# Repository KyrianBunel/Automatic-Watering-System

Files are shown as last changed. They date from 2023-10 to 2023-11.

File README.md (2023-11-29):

# Automatic-Watering-System
Esp32-based automatic irrigation system capable of controlling up to 6 different zones independently

# Features :
- Create a wifi access point to enter wifi information
- Automatically connects to the local network if available
- Compatible with a weather station included in the project to collect temperature, humidity and brightness data, also features a rain sensor
- Able to use up to 3 soil moisture sensors
- Controllable through a web page (LOCAL_IP_ADDRESS/accueil ex : 192.168.1.10/accueil)
    - 3 operating modes :
  
          - MANU -> allows manual control of the 6 valves independently; once the selected valve is active, it can be deactivated only if the user does it manually.
          - AUTO -> uses weather station and soil moisture sensors to automatically trigger a 15-minute watering cycle.
          - PROG -> allows the user to enter information such as watering start and end date, watering duration, recurrence and watering time for each valve via a form.
- Ability to view the current program and sensors values via a dashboard page (LOCAL_IP_ADDRESS/dashboard ex : 192.168.1.10/dashboard)
- Compatible with arduino OTA (update through the local network)
- Automatic watering stop in case of rain (except in MANU mode)
- Transmits sensor data hourly to a Google sheet to create a database

# Future improvements :
- Web pages :
    - Add a settings page
    - Add the possibility of choosing the language (French only for the moment)
    - Add the ability to modify the ID of Google Sheet page in the web interface
    - Add the possibility to modify the number of valve used
- Database :
    - Improve the data sent as the total duration of watering during the last hour to be able to deduct the cost of watering per month and per year
- PCB :
    - Upgrade to an ESP32-WROOM-32UE to add an external antenna and increase the WiFi connection range
    - Move mounting holes & components away from board edge
    - Increase mounting hole size to M3
    - Move decoupling capacitors closer to power supply pins
    - Add a differential pair to the usb port
    - Improve the DC-DC Buck Converter design (produce heat + noise coming from the inductance during current peaks)

# How to start up :
### Home page & Dashboard
- Download the code and upload it to the ESP 32
Capture d’écran 2023-11-27 à 16 22 07

- Press the reset button on the PCB

- Go to the phone settings and connect to the Wifi network: ArrosageAUTO_XXX
- Wait for a web page to open. If the web page doesn't open automatically, go to your browser and type "192.168.4.1"
- Click on "Configure WiFi"
- select your wifi network and enter your password
- Click on "Save"
- And you're done, you can now access the following web pages: LOCAL_IP_ADDRESS/accueil & LOCAL_IP_ADDRESS/dashboard

### Dadabase
- Download the following file [here](https://docs.google.com/spreadsheets/d/1MzfrYDloWlxmfWAgQVE4hzFRyIgfXsLG/edit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) and place it in your personal directory
- Click on "file" -> "save in google sheet format"
Capture d’écran 2023-11-27 à 15 38 50

- Then click on "extensions" -> "apps script" and paste the following code :
Capture d’écran 2023-11-27 à 15 45 44

```
var sheet_id = "YOUR_GOOGLE_SHEET_ID";
var sheet_name = "ArrosageAUTO_data";
function doGet(e){
var ss = SpreadsheetApp.openById(sheet_id);
var sheet = ss.getSheetByName(sheet_name);

var date = e.parameter.date;
var temperature = e.parameter.temperature;
var humidite = e.parameter.humidite;
var luminosite = e.parameter.luminosite;
var moistureSensor1 = e.parameter.moistureSensor1;
var moistureSensor2 = e.parameter.moistureSensor2;
var moistureSensor3 = e.parameter.moistureSensor3;

sheet.appendRow([date,temperature, humidite, luminosite, moistureSensor1, moistureSensor2, moistureSensor3]);
}
```

- Click on "deploy" -> "New deployment" add a description and click "OK"
Capture d’écran 2023-11-27 à 15 22 52

# Additional material required :
- DHT22 temperature and humidity sensor
- Capacitive moisture sensor (3 maximum)
- 9V 24V tranformer (depending on your instlation)
- Rain sensor
- Wi-Fi network (a powerful network to allow pages to load faster)

# Web pages :
### Home page & Dashboard
Capture d’écran 2023-11-24 à 09 25 02

### Extract from the database
Capture d’écran 2023-11-24 à 09 27 08

(the data displayed is random, as no sensor was connected to the board)

# PCB :
Capture d’écran 2023-11-24 à 10 55 46

You can directly order the PCB via this link: https://www.pcbway.com/project/shareproject/Automatic_Watering_System_7e1279b2.html

# Weather station :

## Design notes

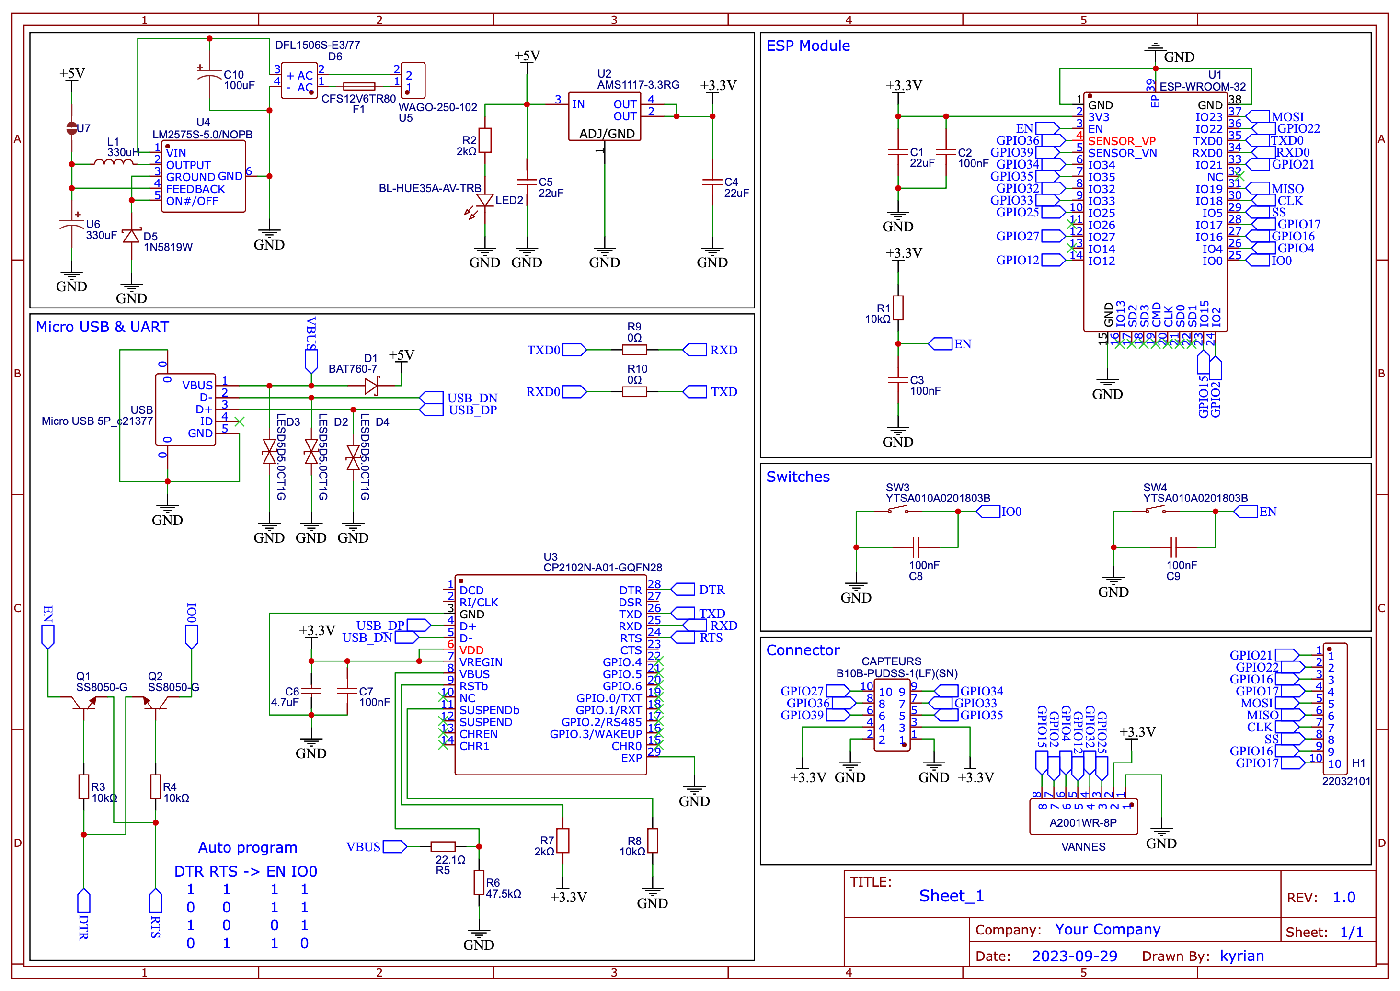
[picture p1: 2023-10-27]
PCB/Schematic_Arrosage automatique_2023-10-27.png

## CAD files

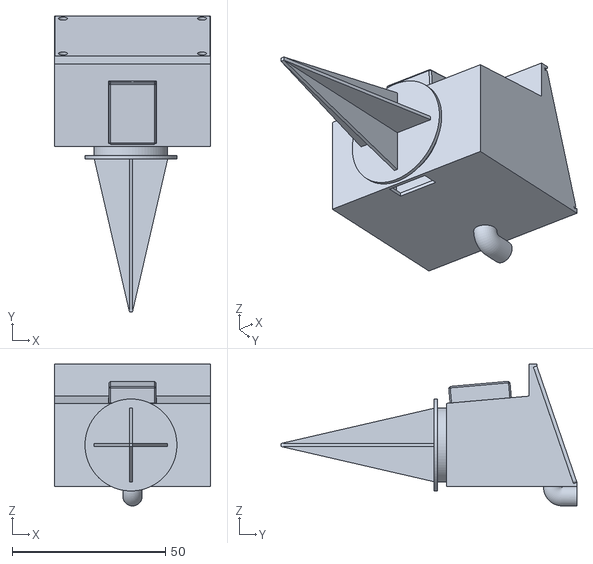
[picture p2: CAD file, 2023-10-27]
3D Models/weather station/assemblage v7.stl
51.0 x 96.6 x 46.3

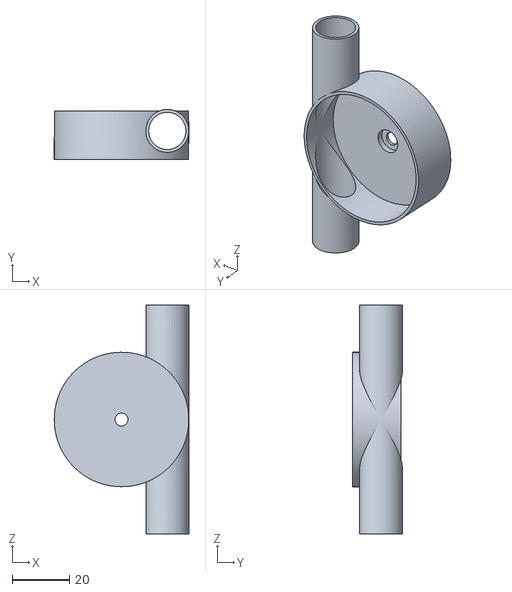
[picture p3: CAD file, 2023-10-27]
3D Models/flow meter/case V2 v1.stl
47.0 x 17.5 x 80.0

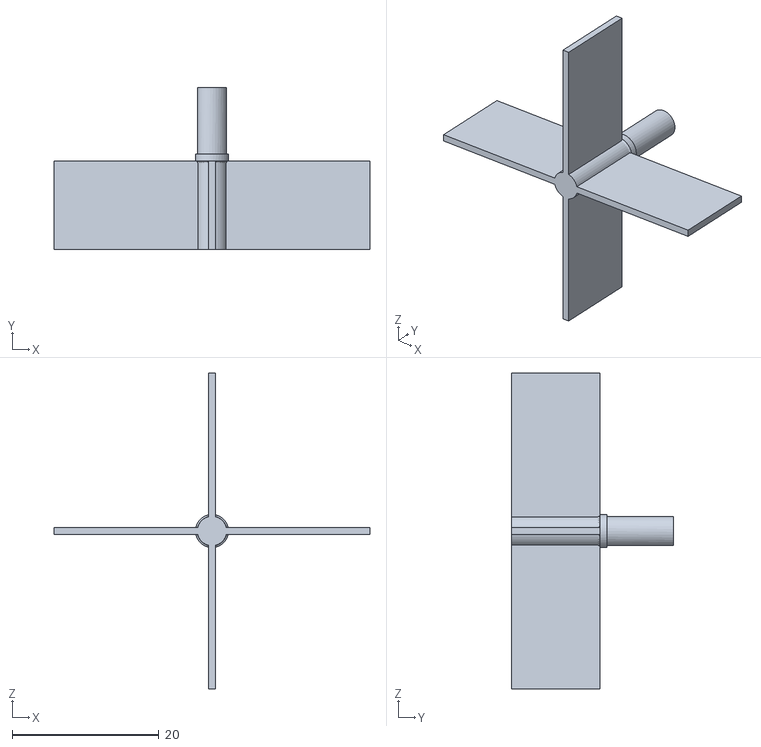
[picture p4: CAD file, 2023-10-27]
3D Models/flow meter/prop V2 v4.stl
43.0 x 22.0 x 43.0

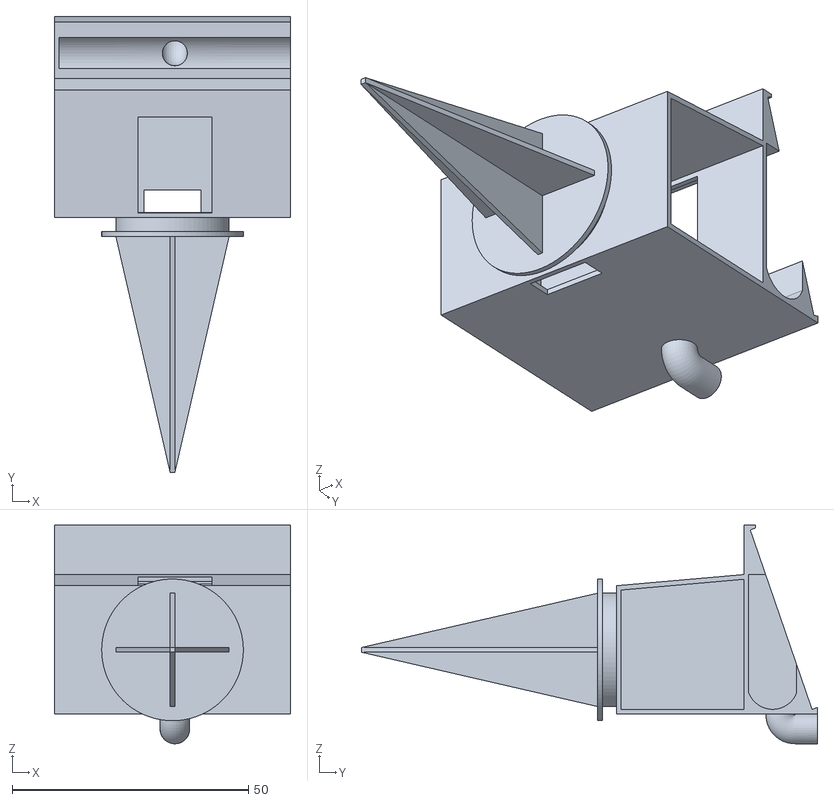
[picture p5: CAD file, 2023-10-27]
3D Models/weather station/station météo v7.stl
50.0 x 96.6 x 46.3

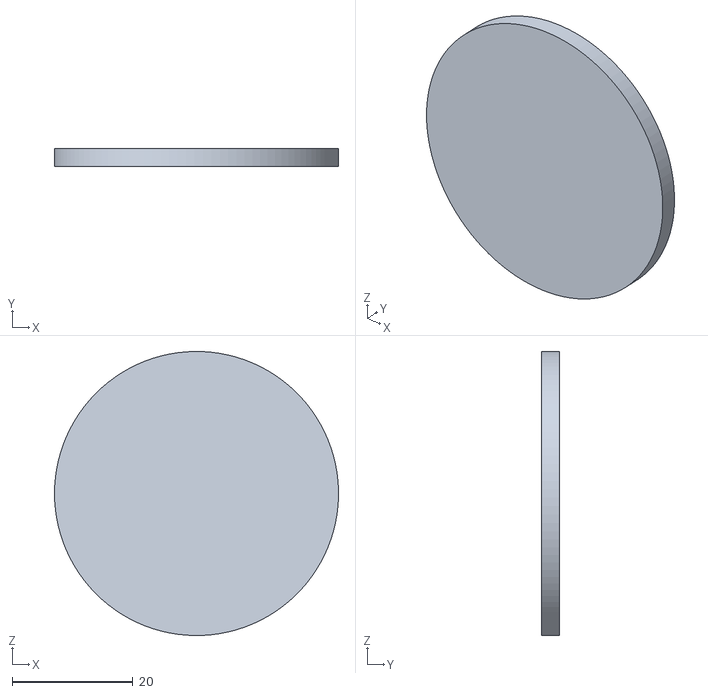
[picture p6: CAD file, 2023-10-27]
3D Models/flow meter/COVER V2 v1.stl
47.0 x 3.00 x 47.0

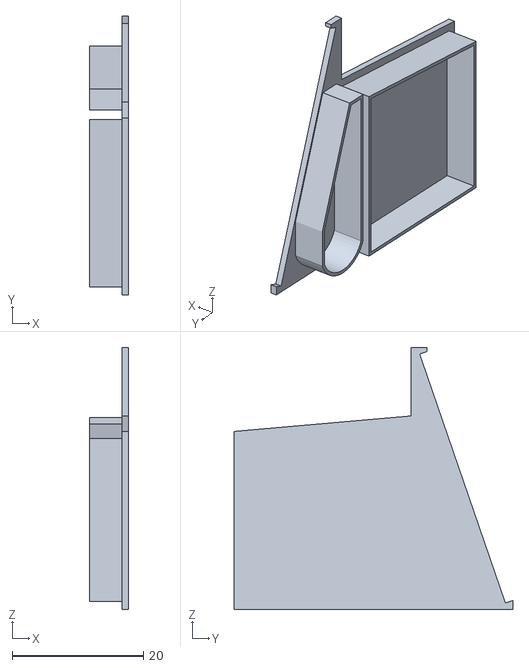
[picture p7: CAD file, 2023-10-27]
3D Models/weather station/side v3.stl
6.00 x 42.6 x 40.0

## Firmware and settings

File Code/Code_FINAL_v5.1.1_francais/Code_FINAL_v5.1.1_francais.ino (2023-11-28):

/*

...............................BIBLIOTHEQUES...............................

*/
#include <WiFi.h>
#include <WiFiManager.h>  // https://github.com/tzapu/WiFiManager
#include <WebServer.h>
#include <ArduinoOTA.h>
#include "DHT.h"
#include <HTTPClient.h>
#include "time.h"

// Google script ID
String GOOGLE_SCRIPT_ID = "YOUR_GOOGLESHEET_ID";  // change Gscript ID

#define DHTPIN 27
#define DHTTYPE DHT22

DHT dht(DHTPIN, DHTTYPE);
struct tm timeinfo;

/*

...............................VARIABLES...............................

*/
String version_logiciel = "5.1.1_fr";    // version du logiciel

const char *ssid = "****";            // SSID WiFI
const char *password = "****";        // Mot de passe WiFi

WebServer server(80);  // Server sur le port 80 (page web)

const char *ntpServer = "pool.ntp.org";  // adresse du serveur NTP
const long gmtOffset_sec = 3600 * 2;     // fuseau horraire (paris)
const int daylightOffset_sec = 3600 * 0;

int SeuilHumidite = 10;  // humididé dans le sol
float SeuilTemperatureMAX = 25.00;
float SeuilTemperatureMIN = 15.00;
int SeuilHumidity = 40.00;  // humidité dans l'air

int TimerAUTO = 0;       // Mesurer le temps d'arrosage en mode AUTO
int delayAUTO = 600000;  // temps d'arrosage en mode AUTO (en ms)
int ModeAuto = 1;        // activation ou non de l'arrosage en mode auto
int JourArrosage;

int bpVanne1 = 0;  // Bouton vanne 1 du mode MANU
int bpVanne2 = 0;  // Bouton vanne 2 du mode MANU
int bpVanne3 = 0;  // Bouton vanne 3 du mode MANU

int MoistureSensor1;  // Capteur d'humidité dans le sol 1
int MoistureSensor2;  // Capteur d'humidité dans le sol 2
int MoistureSensor3;  // Capteur d'humidité dans le sol 3

int pluie;        // Valeur du capteur de pluie
String StrPluie;  // Valeur du capteur de pluie (True/False)

float humidity;     // Valeur humidité
float temperature;  // Valeur température

int luminosite;  // Valeur du capteur de luminosité

int Hour;   // heure actuelle
int Min;    // minute actuelle
int Sec;    // seconde actuelle
int Day;    // jour actuel
int Month;  // mois actuel
int Year;   // année actuelle

int en;

#define vanne1 12        // Vanne 1 sur GPIO12 de l'esp
#define vanne2 32        // Vanne 2 sur GPIO32 de l'esp
#define vanne3 25        // Vanne 3 sur GPIO25 de l'esp
#define CapteurPluie 36  // Capteur de pluie sur GPIO36 de l'esp

char StrHour[40];                                                          // formattage de l'heure en chaîne de caractère
char StrDate[40];                                                          // formattage de la date en chaîne de caractère
char HtmlON[50] = "<div class='rectangleON'>ON</div>";                     // afficher un carré vert marqué ON
char HtmlOFF[50] = "<div class='rectangleOFF'>OFF</div>";                  // afficher un carré rouge marqué OFF
char HtmlDISABLED[50] = "<div class='rectangleDISABLED'>DÉSACTIVÉ</div>";  // afficher un carré violet marqué DISABLED
char HtmlZone1[50];                                                        // afficher état de la zone 1 dans le dashboard
char HtmlZone2[50];                                                        // afficher état de la zone 2 dans le dashboard
char HtmlZone3[50];                                                        // afficher état de la zone 3 dans le dashboard

float usagePercentage;  // Utilisation de la mémoire en %

String mode = "MANU";  // Initialisation de la variable "mode" (valeur par défaut = MANU)

String HTMLtabl;  // Initialisation de la viriable tabl (calendrier)

/* Date de début */
String StrDateDebut;   // enregistrer la date de début rentré dans le formulaire
String StrStartDay;    // Jour de départ (string)
String StrStartMonth;  // Mois de départ (string)
String StrStartYear;   // Année de départ (string)
int StartDay;          // Jour de départ (int)
int StartMonth;        // Mois de départ (int)
int StartYear;         // Année de départ (int)

/* Date de fin */
String StrDateFin;   // enregistrer la date de début rentré dans le formulaire
String StrEndDay;    // Jour de fin (string)
String StrEndMonth;  // Mois de fin (string)
String StrEndYear;   // Année de fin (string)
int EndDay;          // Jour de fin (int)
int EndMonth;        // Mois de fin (int)
int EndYear;         // Année de fin (int)

String StrDuree;  // Dureé du programme (string)
int duree;        // Dureé du programme (int)

String StrRecurrence;  // Récurence (string)
int recurrence;        // Récurence (int)

/* Zone 1 */
String StrZone1;  // Activation de la zone 1 ou non
String StrDebut1;
String StrHeureDebut1;   // Heure de début (string)
String StrMinDebut1;     // Minute de début (string)
char IntervalZone1[40];  // interval d'arrosage (chaîne de carractère)
int HeureDebut1;         // Heure de début (int)
int MinDebut1;           // Minute de début (int)
int EndMin1;             // Minute de fin (int)
int EndHour1;            // Heure de fin (int)

/* Zone 2 */
String StrZone2;  // Activation de la zone 2 ou non
String StrDebut2;
String StrHeureDebut2;   // Heure de début (string)
String StrMinDebut2;     // Minute de début (string)
char IntervalZone2[40];  // interval d'arrosage (chaîne de carractère)
int HeureDebut2;         // Heure de début (int)
int MinDebut2;           // Minute de début (int)
int EndMin2;             // Minute de fin (int)
int EndHour2;            // Heure de fin (int)

/* Zone 3 */
String StrZone3;  // Activation de la zone 3 ou non
String StrDebut3;
String StrHeureDebut3;   // Heure de début (string)
String StrMinDebut3;     // Minute de début (string)
char IntervalZone3[40];  // interval d'arrosage (chaîne de carractère)
int HeureDebut3;         // Heure de début (int)
int MinDebut3;           // Minute de début (int)
int EndMin3;             // Minute de fin (int)
int EndHour3;            // Heure de fin (int)

/*

...............................FONCTIONS...............................

*/
/* Calculer le premier jour du mois (Algorithme de Zeller) */
int calculerPremierJour(int annee, int mois) {
  int a = (14 - mois) / 12;
  int y = annee - a;
  int m = mois + 12 * a - 2;
  int jour = (1 + y + y / 4 - y / 100 + y / 400 + (31 * m) / 12) % 7;
  jour--;
  return jour;  // Retourne le jour de la semaine
}

/* Calculer le nombre de jours en fonction du mois */
int getNumberOfDays(int year, int month) {
  switch (month) {
    case 1:   // Janvier
    case 3:   // Mars
    case 5:   // Mai
    case 7:   // Juillet
    case 8:   // Août
    case 10:  // Octobre
    case 12:  // Décembre
      return 31;
    case 4:   // Avril
    case 6:   // Juin
    case 9:   // Septembre
    case 11:  // Novembre
      return 30;
    case 2:  // Février
      if ((year % 4 == 0 && year % 100 != 0) || (year % 400 == 0)) {
        return 29;  // Année bissextile
      } else {
        return 28;
      }
    default:
      return 0;  // Mois invalide
  }
}

void sendData() {
  String urlFinal = "https://script.google.com/macros/s/" + GOOGLE_SCRIPT_ID + "/exec?" + "date=" + Day + "/" + Month + "/" + Year + "_" + String(Hour) + ":" + String(Min) + ":" + String(Sec) + "&temperature=" + String(temperature) + "&humidite=" + String(humidity) + "&luminosite=" + String(luminosite) + "&moistureSensor1=" + String(MoistureSensor1) + "&moistureSensor2=" + String(MoistureSensor2) + "&moistureSensor3=" + String(MoistureSensor3);
  HTTPClient http;
  http.begin(urlFinal.c_str());
  http.setFollowRedirects(HTTPC_STRICT_FOLLOW_REDIRECTS);
  int httpCode = http.GET();
  http.end();
}

/* Gestion du bouton "MANU" */
void handleMANU() {
  mode = "MANU";
  server.sendHeader("Location", "/accueil");
  server.send(302, "text/plain", "");  // Envoi d'un code de statut 302 (Redirection) sans contenu
}

/* Gestion du bouton "AUTO" */
void handleAUTO() {
  mode = "AUTO";
  bpVanne1 = 0;
  bpVanne2 = 0;
  bpVanne3 = 0;
  server.sendHeader("Location", "/accueil");
  server.send(302, "text/plain", "");  // Envoi d'un code de statut 302 (Redirection) sans contenu
}

/* Gestion du bouton "PROG" */
void handlePROG() {
  mode = "PROG";
  bpVanne1 = 0;
  bpVanne2 = 0;
  bpVanne3 = 0;
  server.sendHeader("Location", "/accueil");
  server.send(302, "text/plain", "");  // Envoi d'un code de statut 302 (Redirection) sans contenu
}

/* Gestion du bouton Vanne 1 du mode MANU (activation/déactivation de l'arrosage) */
void handleVanne1() {
  if (bpVanne1 == 0 && mode == "MANU") {
    bpVanne1 = 1;
  } else
    bpVanne1 = 0;
  server.sendHeader("Location", "/accueil");
  server.send(302, "text/plain", "");  // Envoi d'un code de statut 302 (Redirection) sans contenu
}

/* Gestion du bouton Vanne 2 du mode MANU (activation/déactivation de l'arrosage) */
void handleVanne2() {
  if (bpVanne2 == 0) {
    bpVanne2 = 1;
  } else
    bpVanne2 = 0;
  server.sendHeader("Location", "/accueil");
  server.send(302, "text/plain", "");  // Envoi d'un code de statut 302 (Redirection) sans contenu
}

/* Gestion du bouton Vanne 3 du mode MANU (activation/déactivation de l'arrosage)*/
void handleVanne3() {
  if (bpVanne3 == 0) {
    bpVanne3 = 1;
  } else
    bpVanne3 = 0;
  server.sendHeader("Location", "/accueil");
  server.send(302, "text/plain", "");  // Envoi d'un code de statut 302 (Redirection) sans contenu
}

/*  Gestion du formulaire du mode PROG  */
void handleSubmit() {
  // Récupération des valeurs du formulaire
  StrDuree = server.arg("duree");
  StrDateDebut = server.arg("dateDebut");
  StrDateFin = server.arg("dateFin");
  StrRecurrence = server.arg("recurrence");
  StrZone1 = server.arg("zone1");
  StrZone2 = server.arg("zone2");
  StrZone3 = server.arg("zone3");
  StrDebut1 = server.arg("heureDebut1");
  StrDebut2 = server.arg("heureDebut2");
  StrDebut3 = server.arg("heureDebut3");



  /* Date de début (conversion str -> int) */
  StrStartDay = StrDateDebut.substring(8, 10);
  StrStartMonth = StrDateDebut.substring(5, 7);
  StrStartYear = StrDateDebut.substring(0, 4);
  StartDay = StrStartDay.toInt();
  StartMonth = StrStartMonth.toInt();
  StartYear = StrStartYear.toInt();

  /* Date de fin (conversion str -> int) */
  StrEndDay = StrDateFin.substring(8, 10);
  StrEndMonth = StrDateFin.substring(5, 7);
  StrEndYear = StrDateFin.substring(0, 4);
  EndDay = StrEndDay.toInt();
  EndMonth = StrEndMonth.toInt();
  EndYear = StrEndYear.toInt();

  /* Durée du programme (conversion str -> int)*/
  duree = StrDuree.toInt();

  /* Récurrence (conversion str -> int) */
  recurrence = StrRecurrence.toInt();

  /* Zone 1 (conversion str -> int) */
  StrHeureDebut1 = StrDebut1.substring(0, 2);
  StrMinDebut1 = StrDebut1.substring(3, 5);
  HeureDebut1 = StrHeureDebut1.toInt();
  MinDebut1 = StrMinDebut1.toInt();

  /* Zone 2 (conversion str -> int) */
  StrHeureDebut2 = StrDebut2.substring(0, 2);
  StrMinDebut2 = StrDebut2.substring(3, 5);
  HeureDebut2 = StrHeureDebut2.toInt();
  MinDebut2 = StrMinDebut2.toInt();

  /* Zone 3 (conversion str -> int) */
  StrHeureDebut3 = StrDebut3.substring(0, 2);
  StrMinDebut3 = StrDebut3.substring(3, 5);
  HeureDebut3 = StrHeureDebut3.toInt();
  MinDebut3 = StrMinDebut3.toInt();

  /* End Min */
  EndMin1 = MinDebut1 + duree;
  EndMin2 = MinDebut2 + duree;
  EndMin3 = MinDebut3 + duree;

  /* End Hour */
  EndHour1 = HeureDebut1;
  EndHour2 = HeureDebut2;
  EndHour3 = HeureDebut3;

  if (EndMin1 >= 60) {
    EndMin1 = EndMin1 - 60;
    EndHour1++;
  }
  if (EndMin2 >= 60) {
    EndMin2 = EndMin2 - 60;
    EndHour2++;
  }
  if (EndMin3 >= 60) {
    EndMin3 = EndMin3 - 60;
    EndHour3++;
  }

  /* Formattage interval d'arrosage zone 1 */
  if (StrZone1 == "on")
    sprintf(IntervalZone1, "%s""%s""%d""%s""%d",StrDebut1, "-", EndHour1, ":", EndMin1);
  else
    sprintf(IntervalZone1, "%s", " ");

  /* Formattage interval d'arrosage zone 2 */
  if (StrZone2 == "on")
    sprintf(IntervalZone2, "%s""%s""%d""%s""%d",StrDebut2, "-", EndHour2, ":", EndMin2);
  else
    sprintf(IntervalZone2, "%s", " ");

  /* Formattage interval d'arrosage zone 3 */
  if (StrZone3 == "on")
    sprintf(IntervalZone3, "%s""%s""%d""%s""%d",StrDebut3, "-", EndHour3, ":", EndMin3);
  else
    sprintf(IntervalZone3, "%s", " ");

  /* Récupération du mois et de l'année actuelle sur le server NTP */
  Month = timeinfo.tm_mon + 1;
  Year = timeinfo.tm_year + 1900;

  /* Génération du calendrier du mois en cours */
  int premierJour = calculerPremierJour(Year, Month);

  HTMLtabl = "";
  HTMLtabl += "<h2>Planning d'arrosage</h2> <table> <thead><tr> <th>Lun</th> <th>Mar</th> <th>Mer</th> <th>Jeu</th> <th>Ven</th> <th>Sam</th> <th>Dim</th> </tr> </thead> <tbody>";
  int tablDay = 1;
  int offset = 1;
  int numberOfDays = getNumberOfDays(Year, Month);

  int MaxIter;
  if (premierJour == 6 && numberOfDays == 30)
    MaxIter = 7;
  else
    MaxIter = 6;

  for (int a = 1; a < MaxIter; a++) {
    HTMLtabl += "<tr>";
    for (int i = 1; i < 8; i++) {
      int modulo = tablDay % recurrence;
      if (premierJour >= offset || tablDay > numberOfDays) {
        HTMLtabl += "<td></td>";
      } else if (modulo == 0 && tablDay >= StartDay && tablDay <= EndDay) {
        HTMLtabl += "<td class='highlight'>";  // mettre la case en surbrillance
        HTMLtabl += tablDay;
        HTMLtabl += "</td>";
        tablDay++;
      } else {
        HTMLtabl += "<td>";
        HTMLtabl += tablDay;
        HTMLtabl += "</td>";
        tablDay++;
      }
      offset++;
    }
    HTMLtabl += "</tr>";
  }
  server.sendHeader("Location", "/accueil");
  server.send(302, "text/plain", "");  // Envoi d'un code de statut 302 (Redirection) sans contenu
}

/*

...............................PAGES WEB...............................
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
void loop() {

  server.handleClient();  // Maintenir le client actif (pages web)
  ArduinoOTA.handle();    // Maintenir le client actif (OTA)

  pluie = analogRead(CapteurPluie);  // lecture de la valeur du capteur de pluie + gestion du string pour affichage au dashboard
  if (pluie >> 1)
    StrPluie = "True";
  else
    StrPluie = "False";

  MoistureSensor1 = map(analogRead(35), 0, 4095, 100, 0);  // lecture de la valeur de capteur de pluie + convertion 0,4095->0,100 (%)
  MoistureSensor2 = map(analogRead(33), 0, 4095, 100, 0);  // lecture de la valeur de capteur de pluie + convertion 0,4095->0,100 (%)
  MoistureSensor3 = map(analogRead(34), 0, 4095, 100, 0);  // lecture de la valeur de capteur de pluie + convertion 0,4095->0,100 (%)
  //luminosite = map(analogRead(39), 0, 4095, 10000, 0);     // lecture de la valeur de capteur luminosité + convertion 0,4095->10000,0 (W/m^2)
  luminosite = analogRead(39);

  humidity = dht.readHumidity();        // Mesure de l'humidité + rectification de l'erreur
  temperature = dht.readTemperature();  // Mesure de la température + rectification de l'erreur

  Hour = timeinfo.tm_hour;         // Récupération de l'heure sur le serveur NTP
  Min = timeinfo.tm_min;           // Récupération des minutes sur le serveur NTP
  Sec = timeinfo.tm_sec;           // Récupération des secondes sur le serveur NTP
  Day = timeinfo.tm_mday;          // Récupération du jour sur le serveur NTP
  Month = timeinfo.tm_mon + 1;     // Récupération du mois sur le serveur NTP
  Year = timeinfo.tm_year + 1900;  // Récupération de l'année sur le serveur NTP

  sprintf(StrHour, "%d"
                   "%s"
                   "%d"
                   "%s"
                   "%d",
          Hour, ":", Min, ":", Sec);  // Formattage de l'horloge pour affichage sur le dashboard
  sprintf(StrDate, "%d"
                   "%s"
                   "%d"
                   "%s"
                   "%d",
          Day, "-", Month, "-", Year);  // Formattage de la date pour affichage sur le dashboard

  if (!getLocalTime(&timeinfo)) {  // Impossible d'obtenir la date et l'heure
    Serial.println("Failed to obtain time");
  }

  /* Conditions mode PROG */
  if (recurrence != 0 && mode == "PROG") {                                                                                                          // vérification du mode et de la récurence (div 0)
    if (Day >= StartDay && Month >= StartMonth && Year >= StartYear) {                                                                              // vérification de la date d'arrosage
      if (StrZone1 == "on" && Day % recurrence == 0 && Hour >= HeureDebut1 && Hour <= EndHour1 && Min >= MinDebut1 && Min < EndMin1 && pluie == 1)  // vérification de l'heure d'arrogage, de la selection de la zone & capteur de pluie
      {
        digitalWrite(vanne1, LOW);
        sprintf(HtmlZone1, "%s", HtmlON);
      } else {
        sprintf(HtmlZone1, "%s", HtmlOFF);
        digitalWrite(vanne1, HIGH);
      }
      if (StrZone2 == "on" && Day % recurrence == 0 && Hour >= HeureDebut2 && Hour <= EndHour2 && Min >= MinDebut2 && Min < EndMin2 && pluie == 1)  // vérification de l'heure d'arrogage, de la selection de la zone & capteur de pluie
      {
        digitalWrite(vanne2, LOW);
        sprintf(HtmlZone2, "%s", HtmlON);
      } else {
        sprintf(HtmlZone2, "%s", HtmlOFF);
        digitalWrite(vanne2, HIGH);
      }
      if (StrZone3 == "on" && Day % recurrence == 0 && Hour >= HeureDebut3 && Hour <= EndHour3 && Min >= MinDebut3 && Min < EndMin3 && pluie == 1)  // vérification de l'heure d'arrogage, de la selection de la zone & capteur de pluie
      {
        digitalWrite(vanne3, LOW);
        sprintf(HtmlZone3, "%s", HtmlON);
      } else {
        sprintf(HtmlZone3, "%s", HtmlOFF);
        digitalWrite(vanne3, HIGH);
      }
    }

    if (Min >= EndMin1 && StrZone1 == "on") {
      digitalWrite(vanne1, HIGH);
      sprintf(HtmlZone1, "%s", HtmlOFF);
    }
    if (Min >= EndMin2 && StrZone2 == "on") {
      digitalWrite(vanne2, HIGH);
      sprintf(HtmlZone2, "%s", HtmlOFF);
    }
    if (Min >= EndMin3 && StrZone3 == "on") {
      digitalWrite(vanne3, HIGH);
      sprintf(HtmlZone3, "%s", HtmlOFF);
    }

    if (StrZone1 == "") {                      // Zone 1 non sélectionnée
      sprintf(HtmlZone1, "%s", HtmlDISABLED);  // afficher comme désactivée dans le dashboard
    }
    if (StrZone2 == "") {                      // Zone 2 non sélectionnée
      sprintf(HtmlZone2, "%s", HtmlDISABLED);  // afficher comme désactivée dans le dashboard
    }
    if (StrZone3 == "") {                      // Zone 3 non sélectionnée
      sprintf(HtmlZone3, "%s", HtmlDISABLED);  // afficher comme désactivée dans le dashboard
    }
  }

  /* Conditions mode MANU */
  else if (mode == "MANU") {  // vérification du mode
    if (bpVanne1 == 1) {
      digitalWrite(vanne1, LOW);
      sprintf(HtmlZone1, "%s", HtmlON);
    } else {
      digitalWrite(vanne1, HIGH);
      sprintf(HtmlZone1, "%s", HtmlOFF);
    }
    if (bpVanne2 == 1) {
      digitalWrite(vanne2, LOW);
      sprintf(HtmlZone2, "%s", HtmlON);
    } else {
      digitalWrite(vanne2, HIGH);
      sprintf(HtmlZone2, "%s", HtmlOFF);
    }
    if (bpVanne3 == 1) {
      digitalWrite(vanne3, LOW);
      sprintf(HtmlZone3, "%s", HtmlON);
    } else {
      digitalWrite(vanne3, HIGH);
      sprintf(HtmlZone3, "%s", HtmlOFF);
    }
  }

  /* Conditions mode AUTO (en cours) */
  else if (mode == "AUTO") {  // vérification du mode
    if (ModeAuto == 1 && pluie <= 200 && MoistureSensor1 <= SeuilHumidite && temperature < SeuilTemperatureMAX && temperature > SeuilTemperatureMIN && humidity < SeuilHumidity) {
      digitalWrite(vanne1, LOW);
      sprintf(HtmlZone1, "%s", HtmlON);
      TimerAUTO++;
      JourArrosage = Day;
    }
    if (TimerAUTO >= delayAUTO) {
      ModeAuto = 0;
      TimerAUTO = 0;
      digitalWrite(vanne1, HIGH);
      sprintf(HtmlZone1, "%s", HtmlOFF);
    }
    if (Day - JourArrosage >= 2)
      ModeAuto = 1;
  }
  /* Désactivation des vannes si non */
  else {
    digitalWrite(vanne1, HIGH);
    sprintf(HtmlZone1, "%s", HtmlDISABLED);
    digitalWrite(vanne2, HIGH);
    sprintf(HtmlZone2, "%s", HtmlDISABLED);
    digitalWrite(vanne3, HIGH);
    sprintf(HtmlZone3, "%s", HtmlDISABLED);
  }

  if (en == 1 && Min == 0 && Year != 1900) {
    sendData();
    en = 0;
  }
  if (Min == 2)
    en = 1;

  delay(1);  // ajout d'un délais d'une ms pour la stabilité du système
}
